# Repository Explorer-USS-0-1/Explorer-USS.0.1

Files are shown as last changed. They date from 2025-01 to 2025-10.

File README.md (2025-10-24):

# <p align="center"> EXPLORER USS.0.1 </p>

<p align="center">
 
</p>

The goal of this project is to create and learn how a exploration rover can be, how can be built and what we can do with it. We liked the idea to do something that could move anywhere we wanted, on every type of soil and very far away, so we designed and created our personal rover from scratch.

Because we couldn't see it everywhere, we gave to the rover an eye (a camera), so we can see what it sees.

Maybe is not a professional rover, or a competitive one, but for sure with a very limited budget and almost zero starting knowledge, we learned a lot about embedded software and IOT.

>[!Note]
>
>In the [printfile folder](/Rover_chassis_and_tools_printfiles) there are a lot of files, cause during the desing phase we scraped and redesinged a lot of time the rover prototype.

## REQUIREMENTS

#### Hardware

To build and use this project, you need the following hardware:

- 1x Texas Instruments MSP432P401R microcontroller
- 1x [Educational BoosterPack MKII](https://www.ti.com/tool/BOOSTXL-EDUMKII)
- 2x [Esp32-Wroom-32D](https://www.espressif.com/sites/default/files/documentation/esp32-wroom-32d_esp32-wroom-32u_datasheet_en.pdf)
- 1x [Esp32-CAM](https://media.digikey.com/pdf/Data%20Sheets/DFRobot%20PDFs/DFR0602_Web.pdf)
- 4x DC Motors (driving wheels)
- 2x L298N motor's driver
- 2x micro servomotor
- A 12 volt 3.5 Amp powersource (for the motor controller board)
- 2x 5 volt powersource (1 for the Esp-Cam, 1 for the Servomotors and Esp32)
  - If you want, you can use a voltage step down board (we did this due to time and budget costrains)
- 2x [rover track outer frame](Rover_chassis_and_tools_printfiles/ProtoTank_TrackOuterFrame.stl)
- 2x [rover track inner frame](Rover_chassis_and_tools_printfiles/ProtoTank_trackinnerFrame.stl)
- 2x [full rover tracks](Rover_chassis_and_tools_printfiles/track_1_5.stl)
- 6x [cog](Rover_chassis_and_tools_printfiles/ProtoTank_Cog.stl)
- [Rover base frame](Rover_chassis_and_tools_printfiles/ProtoTank_baseFrame.stl)
- 2x [L298N driver holder](Rover_chassis_and_tools_printfiles/L298N%20holder%20V3.stl)
- [Rover top frame](Rover_chassis_and_tools_printfiles/ProtoTank_TopFrame.stl)
- [Base for camera structure](Rover_chassis_and_tools_printfiles/CAMTANKFINAL.stl)
- [Pan & tilt arm base](Rover_chassis_and_tools_printfiles/Pan-tilt-plataforma_finale.stl)
- [Pan part for "turret"](Rover_chassis_and_tools_printfiles/Pan-tilt-tapa_finale.stl)
- [Tilt part for "turret"](Rover_chassis_and_tools_printfiles/platformafinalv2.3.stl)
- [Esp32-Cam holder](Rover_chassis_and_tools_printfiles/finalemnte%20v2.stl)
- [Power System Holder](Rover_chassis_and_tools_printfiles/power%20supply%20holder%20v4.stl)
- Jumper wires of all types (M/F , M/M , F/F)
- A lot of screws and bolts
- 1 Usb-C cable
- PLA of two different colors ( one for tracks, one for everything else)
<p align="center">
  

  

  
</p>

#### Software
- [Code Composer Studio](https://www.ti.com/tool/CCSTUDIO) Integrated Development Environment (IDE)
- [MSP432 DriverLib](https://www.ti.com/tool/download/SIMPLELINK-MSP432-SDK/3.40.01.02)
- Arduino IDE

>[!IMPORTANT]
>
>The rover is designed to be customizable, our project is just an example.

## PROJECT LAYOUT

```
├───Rover
│   ├───Esp32Cam
│   ├───Final
│   └───MSP + ESP FINAL
│       ├───Debug
│       │   └───LcdDriver
│       ├───LcdDriver
│       └───targetConfigs
├───Rover_chassis_and_tools_printfiles
└───Separate_testing_tools
    ├───Car_Image_State_Machine
    │   ├───Debug
    │   │   └───LcdDriver
    │   ├───LcdDriver
    │   └───targetConfigs
    ├───DC_Motors
    ├───MSP_Tank_Final
    │   ├───Debug
    │   │   └───LcdDriver
    │   ├───LcdDriver
    │   └───targetConfigs
    ├───MSP_Tank_Test
    │   ├───Debug
    │   │   └───LcdDriver
    │   ├───LcdDriver
    │   └───targetConfigs
    ├───Push_buttons
    │   ├───Debug
    │   │   └───LcdDriver
    │   ├───LcdDriver
    │   └───targetConfigs
    └───Servomotors
```

## SETUP

### Hardware setup

The hardware setup requires time and planning, because **all the structural part** of the rover are **3D printed**. We decided to do this to have a light but very strong structure.

>[!Note]
>
>The prints of our project were made with 100% recicled PLA.

#### ROVER

After printing all the files linked in the [**hardware requirements**](#REQUIREMENTS) section ( or any other file in the [Rover_chassis_and_tools_printfile](https://github.com/Dennis-Alberti/IoT-project/tree/main/Rover_chassis_and_tools_printfiles) folder), you can start build up the chassis in this order:
1. Build the track frames (whit the cogs), and put the DC motors in them;
   <p align="center">
        

2. Put the track frames on the baseframe, using screws and bolts to secure the 2 parts, and then put the L298N driver holders in the holes of the base (they should perfectly fit);
3. Use screw and bolts to secure the L298N divers to their holder frames; also connect the motors to the drivers and be sure that the opposing engines have the color order of the cables reversed. At the same time be sure that the motors sharing the track frame have the same cables color order;
    <p align="center">
        
    </p>
4. Use the F/F jumper wires to connect all the motor speed pins to the ESP32-2 (displayed in the [**PIN LAYOUT**](#PIN_LAYOUT) section, ESP32-2 table);
5. Close the chassis whit the rover top frame, then put the tracks in place;
6. Put inside the ESP32-Cam holder the ESP32-Cam, and then build up the "turret" structure with the servomotors;
    <p align="center">
      
    </p>
8. Mount on the rover chassis the "turret" and connect to the Esp32-2 the servomotors (following the same table of the point 4);
    <p align="center">
       
       
    </p>
9. Now is possible put any additional accessory or tool ( from our printfile folder or any custom-made one ).

>[!IMPORTANT]
>
>**To power up everything the same way we did it, check out the [POWER SYSTEM MANAGEMENT](#POWER_SYSTEM_MANAGEMENT) section**

#### JOYSTICK

Connect the MSP432P401R microcontroller whit the ESP32-1 using F/F Jumper wires, following the [ESP32-1 table pin layout](#PIN_LAYOUT).
  <p align="center">
   
  </p>

### Software setup

##### Msp432 Setup
1. Go to the section below (MSP432 DriverLib Setup) to setup the DriverLib to be able to use the [Educational BoosterPack MKII](https://www.ti.com/tool/BOOSTXL-EDUMKII).
2. Connect the MSP with a computer.
3. Go to [`Rover/MSP + ESP FINAL/main.c`](Rover/MSP%20%2B%20ESP%20FINAL/main.c), [`Rover/MSP + ESP FINAL/functions.h`](Rover/MSP%20%2B%20ESP%20FINAL/functions.h) and [`Rover/MSP + ESP FINAL/functions.c`](Rover/MSP%20%2B%20ESP%20FINAL/functions.c) and download the files.
4. Open it in the projects previously created at point 1.
5. Upload and run the code.

##### Esp32-1 Setup  
1. Connect the ESP with a computer.  
2. Go to [`Rover/Final/EspSender.ino`](Rover/Final/EspSender.ino) ,and download the file.   
3. Open it with Arduino IDE and change the variable `broadcastAddress[]` with the address of the ESP connected to the rover (*see [Communication Section](#COMMUNICATION)*).  
4. Upload and run the code.  

##### Esp32-2 Setup  
1. Connect the ESP with a computer.
2. Go to [`Rover/Final/DcandServo.ino`](Rover/Final/DcandServo.ino), and download the file. 
3. Open it with Arduino IDE and install the library: **"ESP32Servo"** by *Kevin Harrington, John K. Bennett*.  
4. Upload and run the code.

##### Esp32-Cam Setup
1. Connect the Esp-cam with a computer.
2. Go to [`Rover/Final/EspSender.ino`](Rover/Esp32Cam) ,download all the files in the folder and create a folder with all of them inside.
3. Open the CameraWebServerEsp32Cam.ino file with Arduino IDE. In the "const char *ssid" and "const char *password" variables (line 39 and 40 of the code) put the name and the password of the wi-fi you're going to use to host the webserver;
4. Upload and run the code.
5. Only for the first time (or everytime you change the host wi-fi), you have to copy the IP ADDRESS, printed in output on the Serial monitor of your pc, and paste it on a browser tab. 

Once you have ensured the connection between the 2 ESP32 (see [COMMUNICATION](#COMMUNICATION) section to know how), and the webserver for the ESP32-CAM is working, you can start to use the rover.
   
## HOW TO USE

The MSP432 code put in action the rover. The initial state shows a white car and the phrase "Welcome Back !". 

<p align="center">

</p>

To start moving the tank, press the S3 button (position right/bottom of the controller), that will put the joystick in TANK mode, displaying the current state on the screen. Now you can move the rover using the joystick.
* UP: move the rover forward.
* DOWN: move the rover backward.
* RIGHT: move the rover right.
* LEFT: move the rover left

<p align="center"> 

</p>

To use the camera and thus entering CAMERA mode, press the S2 button (position right/top of the controller) and use the joystick to point in the desired direction. 
* UP: move the camera up.
* DOWN: move the camera down.
* RIGHT: move the camera right.
* LEFT: move the camera left.
* JOYSTICK BUTTON: reset the camera position to the center.

Pressing the S2 button will the switch again to the TANK mode, and so on.
All this is possible thanks to the handler, that will listen for the interrupt of an action at any moment and send the message to the Esp32-1.

Now you can use EXPLORER USS.0.1 to go everywhere you want, and see what your eyes could never!

>[!Note]
>
> Is possible to test every part of the project separatley, just go in the in the [separate_testing_tools](/Separate_testing_tools) folder, and try whatever you want (for the rover parts, you will need to implememt an external joystick for testing, but not the full one).

## COMMUNICATION

This project is divided into two modules: the **controller** and the **rover**. These modules are connected via ESP-NOW protocol using two ESP32 microcontrollers. All the information originates from the MSP432 microcontroller, which sends it to **ESP32-1**. ESP32-1 then transmits the data to **ESP32-2**, which interprets the messages and sends instructions to the DC motors and servo motors on the rover. The connection between the ESP's is done using the libraries <esp_now.h> and <WiFi.h> in Arduino IDE. 

The decision to use the ESP-NOW protocol is due to the reliability, low energy consumption, high message transfer speed and long range connection.

>[!IMPORTANT]
>
>To set up and use ESP-NOW you need to know the IP address of the Rover's ESP32. Here's a quick tutorial how: https://randomnerdtutorials.com/get-change-esp32-esp8266-mac-address-arduino/

To establish communication between the MSP432 and ESP32-1, we had three options: **I2C**, **UART**, and **SPI**. We chose **UART** because it requires fewer pins and is simpler to implement. Due to the pin layout of the MSP432, we are limited to using UART module **A2**, with pins **3.2 (Rx)** and **3.3 (Tx)**, connected to pins **17 (TX)** and **16 (Rx)** respectively. 

The UART is configured to use the **SMCLK (Sub-Main Clock)** for the following reasons:
1. We are using a low baud rate of **9600**, which does not require a high-frequency clock.
2. Using SMCLK allows the **main clock (MCLK)** to operate independently, freeing it up for other tasks.
3. There is no need to use the main clock, as it is less power-efficient compared to SMCLK.

This setup ensures efficient and reliable communication between the MSP432 and ESP1 while optimizing power consumption and resource allocation.

## PIN LAYOUT

 Table 1: ESP32 connected to MSP432
| **ESP32 Pin** | **MSP432 Pin** | 
|---|---|
| GPIO16 (RX) | P3.3 (TX) | 
| GPIO17 (TX) | P3.2 (RX) |
| GND | GND |
| VIN | 5V | 

 Table 2: ESP32 connected to DC motors and servo motors
| **ESP32 Pin** | **DC motors** | **Servo motors** | **Power System** |
|---|---|---|---|
| 21 | Motor1 Pin1 | - | - |
| 33 | Motor1 Pin2 | - | - |
| 16 | Motor2 Pin1 | - | - |
| 17 | Motor2 Pin2 | - | - |
| 18 | Motor3 Pin1 | - | - |
| 19 | Motor3 Pin2 | - | - |
| 22 | Motor4 Pin1 | - | - |
| 23 | Motor4 Pin2 | - | - |
| 27 | MOTOR1 SPEED | - | - |
| 26 | MOTOR2 SPEED | - | - |
| 14 | MOTOR3 SPEED | - | - |
| 25 | MOTOR4 SPEED | - | - |
| 13 | - | servoX (Signal)  | - |
| 32 | - | servoY (Signal)  | - |
| GND | - | - | GND |
| VIN | - | - | 5V |

 Table 3: MSP432 Pins Axis Joystick with Push Buttons
| **Pin Functions**  | **MSP432 Pin** | 
|--- |---|
| Hori X-axis | P6.0	 | 
| Verti Y-axis | P4.4 |
| Select button | P4.1 |
| S2 button | P5.1 | 
| S3 button | P3.5 | 

## MSP432 DriverLib Setup

First thing to perform is setting up the IDE. For this purpose use [Code Composer Studio](https://www.ti.com/tool/CCSTUDIO) Integrated Development Environment (IDE) and:
- Create a new project, select the MSP432P401R board in the selection tab and give a name to the project.
- Download and extract the [MSP432 DriverLib](https://www.ti.com/tool/download/SIMPLELINK-MSP432-SDK/3.40.01.02) and save in a reachable directory, then do the following action to setup the environment:
   
1. Extract simplelink_msp432p4_sdk_3_40_01_02.zip file.
2. Open CCS and left click on Project Folder to select Properties
3. Select CCS Build
4. Click ARM Compiler and then Include Options
5. Add "simplelink_msp432p4_sdk_3_40_01_02/source" directory to "Add dir to #include search path" window.  
6. Click ARM Linker and File Search Path
7. Add "simplelink_msp432p4_sdk_3_40_01_02/source/ti/devices/msp432p4xx/driverlib/ccs/msp432p4xx_driverlib.lib" to "Include library file..." window

## POWER SYSTEM MANAGEMENT

The power system of our rover it's composed by 4 modules:
1. A 12 Volt 3.5 Ah module to power up the L298N drivers for DC motors. This was obtained by putting in series 8 batteries of 1.5 Volt;
2. A 9 Volt battery connected to a step down voltage board  to power up the servomotors and the ESP32-2;
3. A 5 Volt output powerbank to power up the ESP32-Cam (we decided to do this because the camera drains a lot of power);
4. A 5 volt output powerbank to power up the MSP432 and the connected ESP32-1. 

The first 2 modules are powering up motors connected and controlled by the ESP32-2, so they have to share in common the ground. To do it, we placed the stepdown voltage board on a breadboard using the external channels, which are connected per row throughout the breadboard.
In this way we made a row where the electricity output of the step down board was off, putting instead the external 12 Volt module, and connecting in the parallel row the grounds from the ESP32-2, from the L298N drivers and from the servomotors. In the other external row we set a 5V electricity output so we could power up the ESP32-2 trough the VIN pin and the 2 servomotors (the ESP32 pinout is already described in the [*Communication*](#COMMUNICATION) section).
<p align="center">

</p>

Table 4: Rover power system management  
| **DC motors** | **Servo motors** | **Stepdown board** |
|---|---|---|
| Power | - | 12V - 3.5A (output off) |
| GND | - | GND | 
| - | Power | 5V  (output on) |
| - | GND | GND |

## Link to powerpoint and Youtube video
- Youtube [video](https://youtu.be/4N75zm8ps9I)
- Powerpoint [presentation](https://docs.google.com/presentation/d/1o49VAeFgKbm6rYsIu1tgTplBiTX86RdQqd6DO4X7Q_E/edit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)

## ISSUES.

In this section we want to explain the major difficulties encountered during the project.

One of the main drawbacks was using the MSP432 as a controller. In fact we noticed that the command input had some latency, approximately 500ms. This was also due to the UART connection between the MSP432 and ESP32, followed by the connection via the ESP-NOW protocol. Also using the MSP432 boosterpack limited the possibility to have simultameous movement of camera and rover. But we decided to use the board anyway to challenge us into understanding more complicated boards than Arduino.

Another problem was the lack of knowledge in the field of electronic engineering. In fact we had no prior knowledge about the hardware and power management parts, so we had to study from zero how these worked.

The last drawback was the limited budget, that forced us to use low-cost hardware.

## FUTURE IMPROVEMENTS

- Rebuilding the power system, using only a rechargable Lipo battery to power every part of the rover;
- Upgrading the quality of the sensors, of the motors and of the camera;
- Using only 2 ESP's, one for the controller and one for the movement;
- Implementing simultaneous movement of camera and rover, and also have more freedom in the movements;
- Implementing an automated movement system using ultrasonic sensors and algorithms;
- Implementing an object detection project using the camera;
- Implementing an automated garage for the rover, working as an homestation where it can recharge;
- Implementing some led light, to use the rover also in darker places;
- Implementing a more detailed interface on screen, by creating a menu screen to navigate through the different modes;
- Implementing a timer to register inactivity from the user, causing the system to switch to a sleep mode;
- Using the Pulse Width Modulation to regulate the movement speed based on the position of the controller ( so constantly changing , and not a fixed value);
- Optimize the code; make the code easier to read, more intuitive.

## TEAM MEMBERS

The project was developed in a team and the code was divided into many different areas (Rover, Communications, Graphics, Hardware, ...); each member focused therefore only on certain aspects of the project.

- Riccardo Ferro (Leader)
  - Contributed mainly to the creation of the physical and hardware part of the rover. He designed the layout of the chassis, organized the power system and setted up all the connections of the rover. He also contributed a lot to write the code for motor control (ESP32-2) and also the code for the communication between ESP32-1 and ESP32-2 using the ESP-NOW protocol. He also did the ESP-32 Camera configuration and the final code and documantation review.

- Henrique Graça
  - Contributed mainly to: setup the ESP32-2 connection of the rover; write the code of the ESP32-2 and ESP32-1; UART connection between the MSP432 and ESP32-1. 

- Dennis Alberti
  - Contributed mainly in the creation of the MSP432 code.

- Tiago Silva
  - Contributed mainly in the creation of the MSP432 code and was responsible for video editting of the project's showcase.

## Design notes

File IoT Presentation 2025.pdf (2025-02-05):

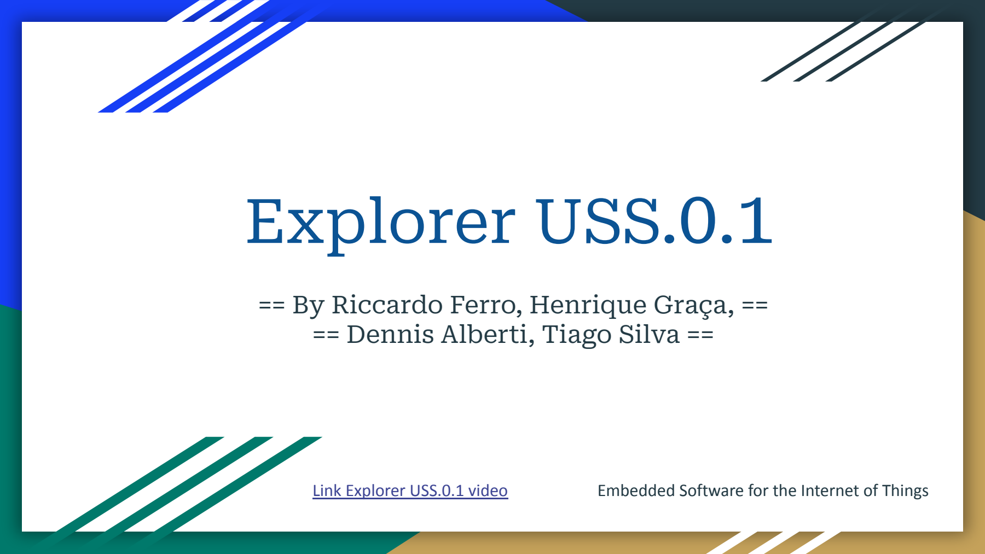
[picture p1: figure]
Explorer USS.0.1; == Dennis Alberti, Tiago Silva ==

## == By Riccardo Ferro, Henrique Graça, ==

Link Explorer USS.0.1 video (https://youtu.be/4N75zm8ps9I) | Embedded Software for the Internet of Things (https://didatticaonline.unitn.it/dol/auth/shibboleth/index.php)

## ROVER & CAMERA - CONTROLLER

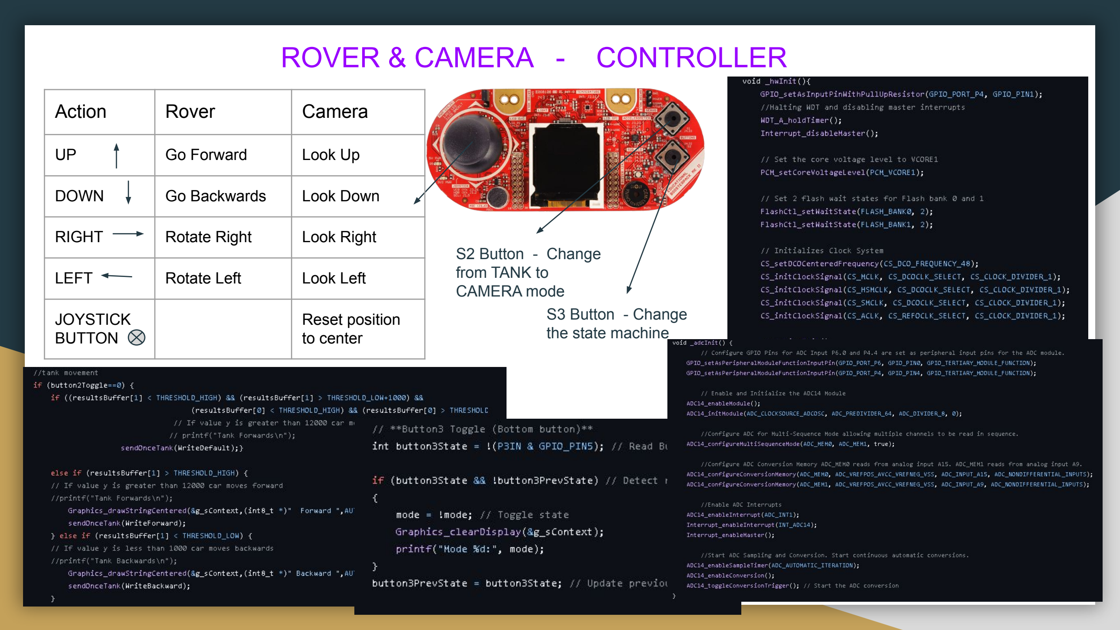
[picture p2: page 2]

S3 Button - Change
the state machine

S2 Button - Change
from TANK to
CAMERA mode
Action | Rover | Camera
UP | Go Forward | Look Up
DOWN | Go Backwards | Look Down
RIGHT | Rotate Right | Look Right
LEFT | Rotate Left | Look Left
JOYSTICK BUTTON | | Reset position to center

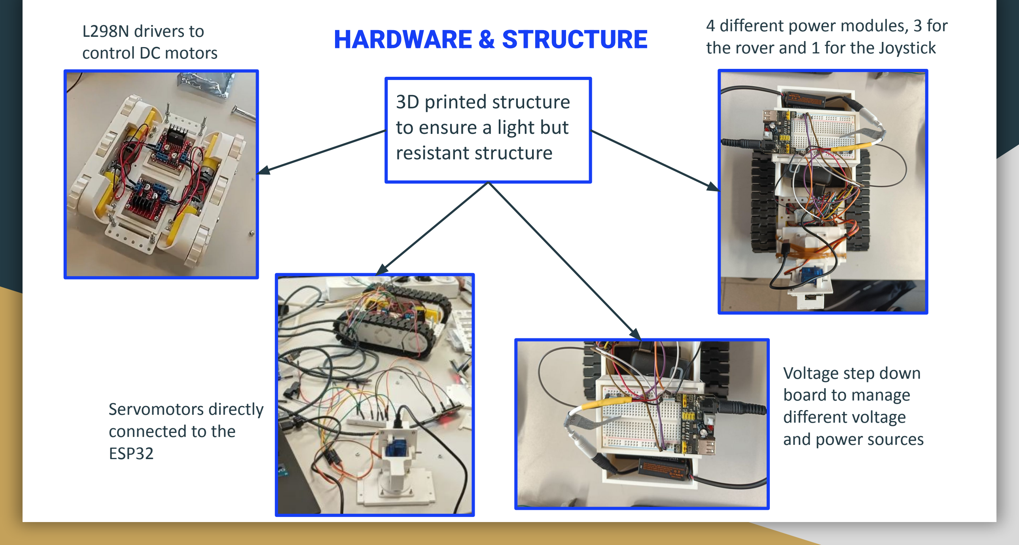
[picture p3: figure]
HARDWARE & STRUCTURE L298N drivers to control DC motors; 4 different power modules, 3 for the rover and 1 for the Joystick; 3D printed structure to ensure a light but resistant structure; Servomotors directly connected to the ESP32; Voltage step down board to manage different voltage and power sources

## MOTORS,DRIVERS AND CAMERA

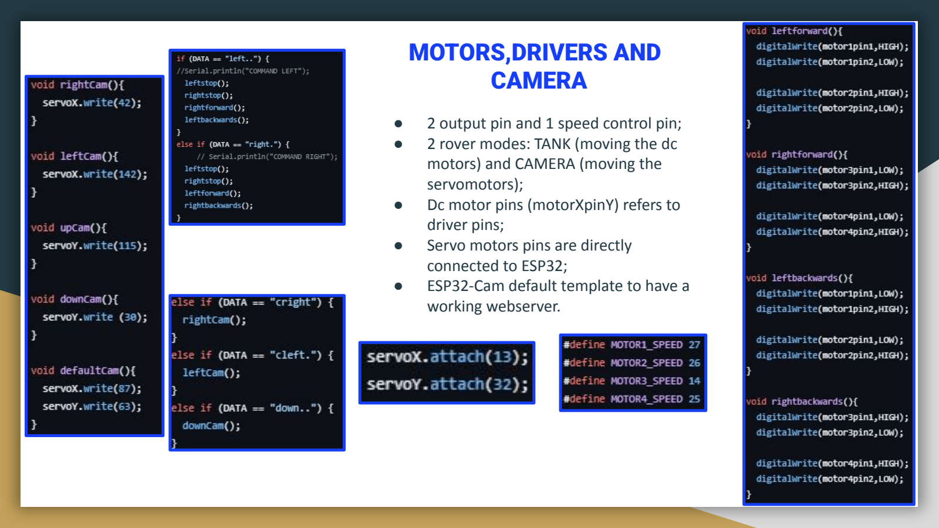
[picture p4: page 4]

- 2 output pin and 1 speed control pin;
- 2 rover modes: TANK (moving the dc motors) and CAMERA (moving the servomotors);
- Dc motor pins (motorXpinY) refers to driver pins;
- Servo motors pins are directly connected to ESP32;
- ESP32-Cam default template to have a working webserver.

## COMMUNICATION MSP

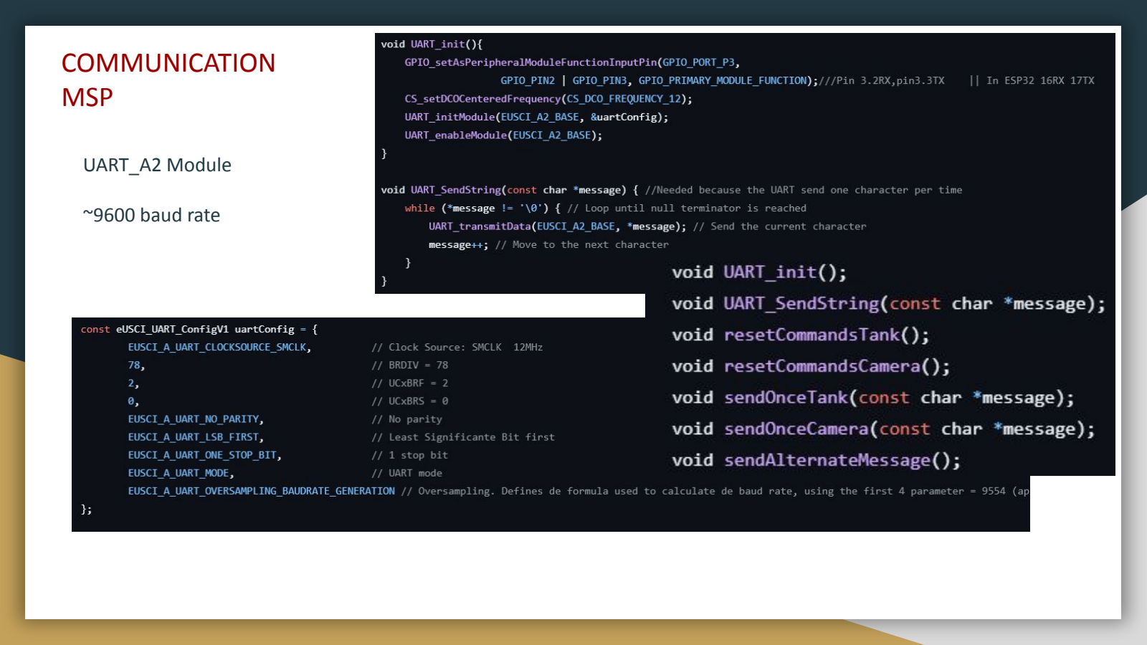
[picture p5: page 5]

UART_A2 Module

~9600 baud rate

## COMMUNICATION

## ESP1

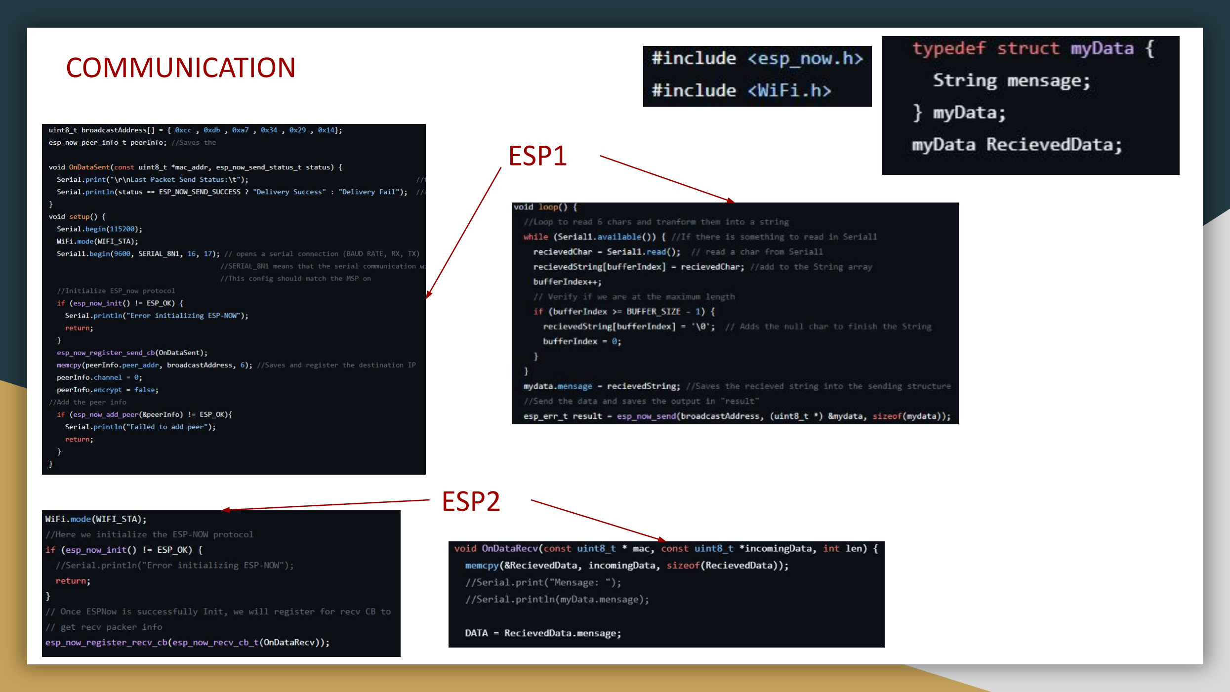
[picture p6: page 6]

## ESP2

## TESTING & FUTURE IMPROVEMENT

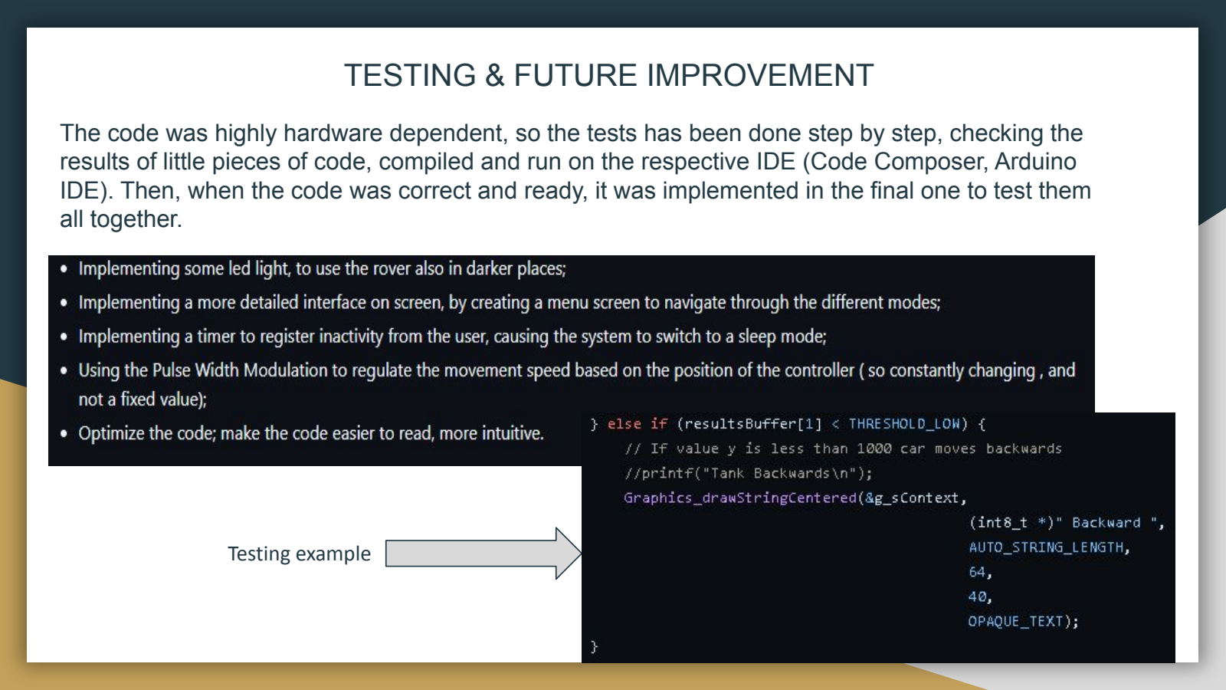
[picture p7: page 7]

The code was highly hardware dependent, so the tests has been done step by step, checking the results of little pieces of code, compiled and run on the respective IDE (Code Composer, Arduino IDE). Then, when the code was correct and ready, it was implemented in the final one to test them all together.

Testing example

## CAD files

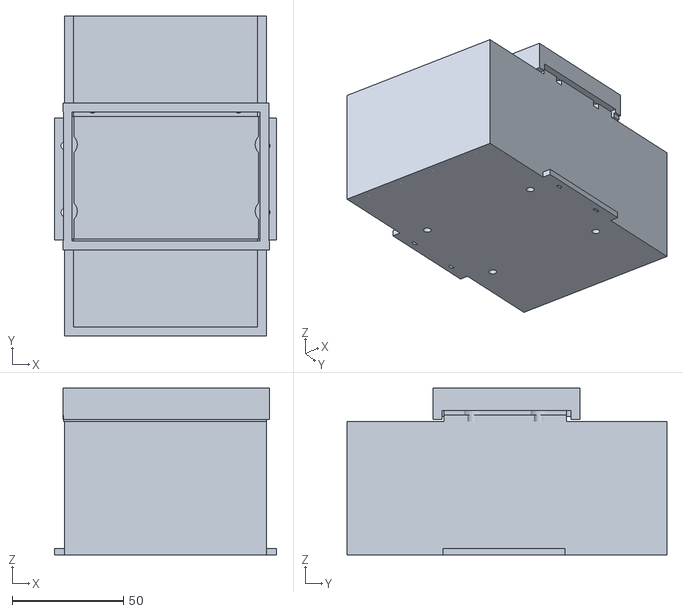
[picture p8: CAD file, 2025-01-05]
Rover_chassis_and_tools_printfiles/powersupply holder v3.stl
100.0 x 144.0 x 75.1

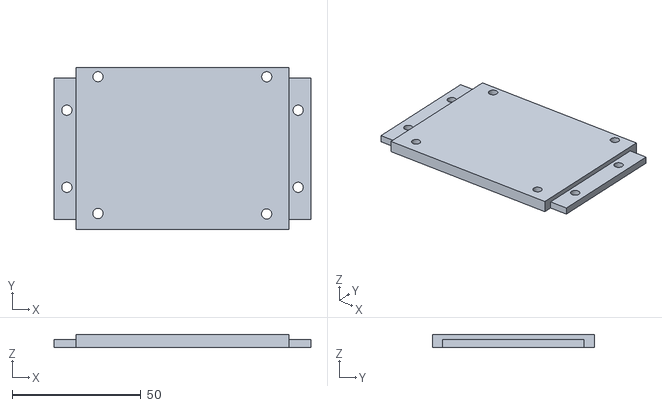
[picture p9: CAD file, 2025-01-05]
Rover_chassis_and_tools_printfiles/Powering System Base.stl
100.0 x 63.2 x 5.00

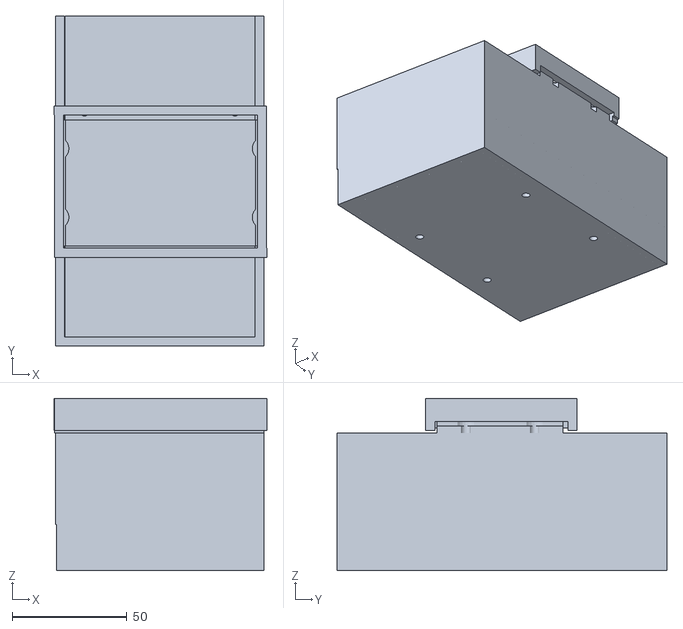
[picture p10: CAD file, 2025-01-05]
Rover_chassis_and_tools_printfiles/power supply holder v4.stl
92.9 x 144.0 x 75.1

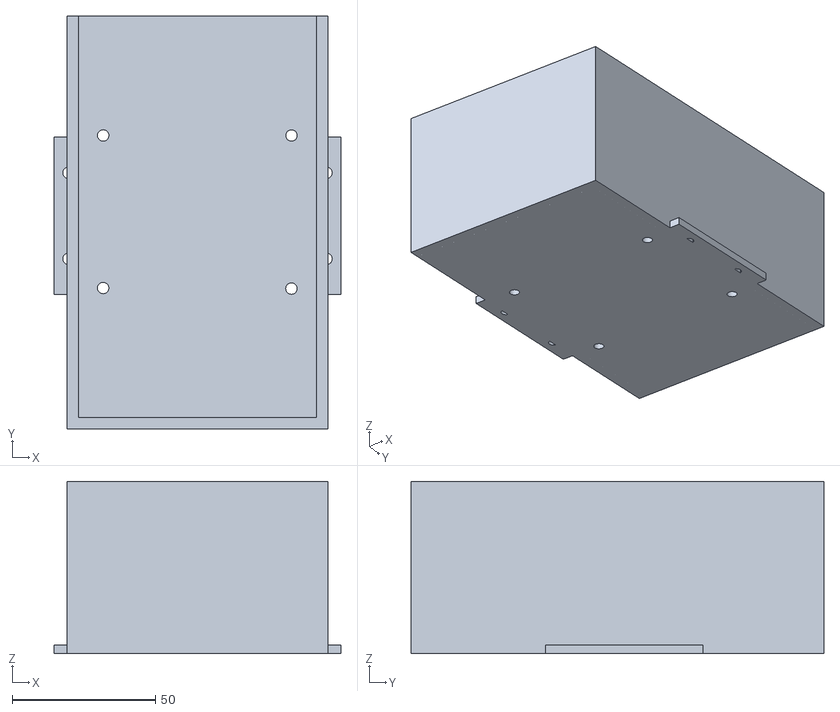
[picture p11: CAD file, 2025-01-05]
Rover_chassis_and_tools_printfiles/temporary power system holder.stl
100.0 x 144.0 x 60.0

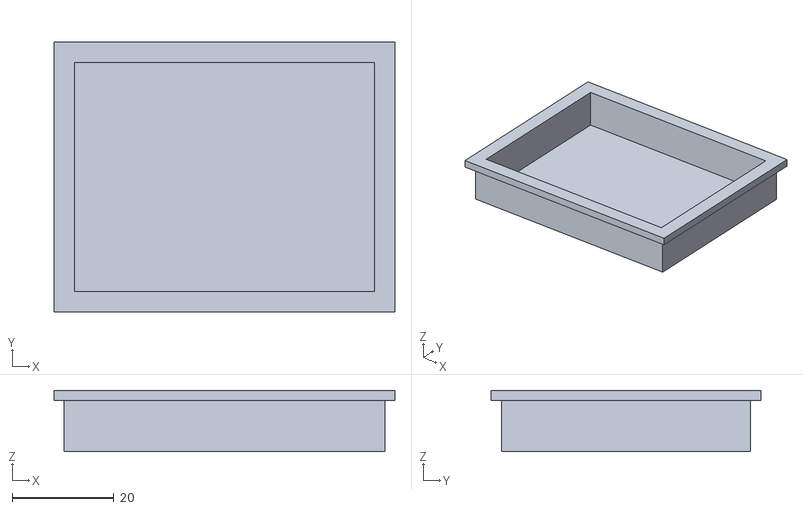
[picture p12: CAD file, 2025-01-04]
Rover_chassis_and_tools_printfiles/Accessory_baseTray.stl
67.0 x 53.0 x 12.0

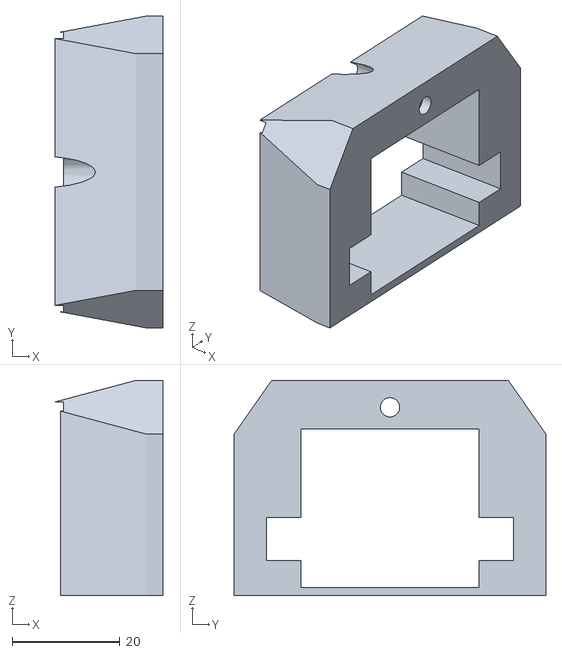
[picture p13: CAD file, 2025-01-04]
Rover_chassis_and_tools_printfiles/CAMERACOVE V$.stl
20.0 x 58.0 x 40.0

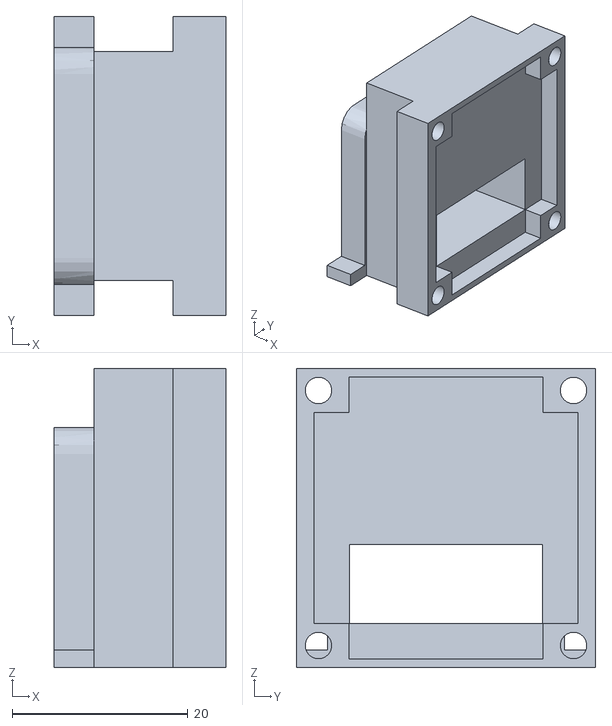
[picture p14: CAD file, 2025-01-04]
Rover_chassis_and_tools_printfiles/My Cmaera holder v1.stl
19.6 x 34.0 x 34.0

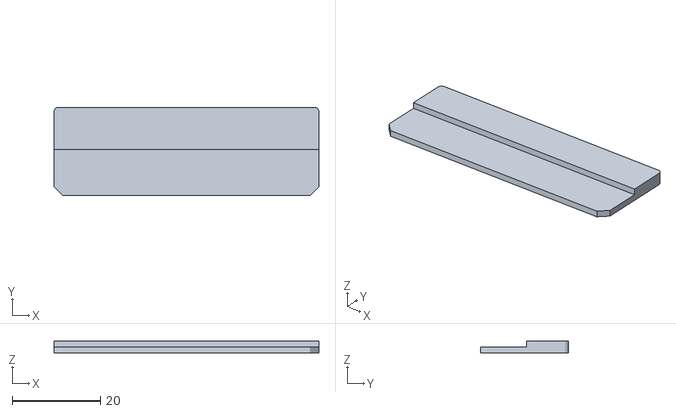
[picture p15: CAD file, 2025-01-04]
Rover_chassis_and_tools_printfiles/TheBackFellOffItsNotSupposedToDoThat.stl
60.0 x 20.0 x 2.80

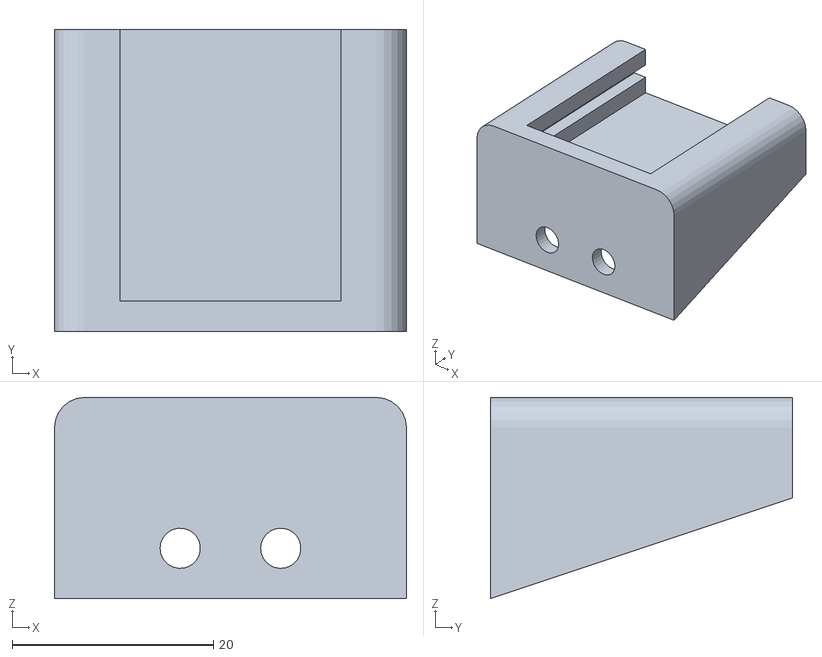
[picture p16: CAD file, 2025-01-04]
Rover_chassis_and_tools_printfiles/Accessory_Static_RPi_CameraHolder.stl
35.0 x 30.0 x 20.0

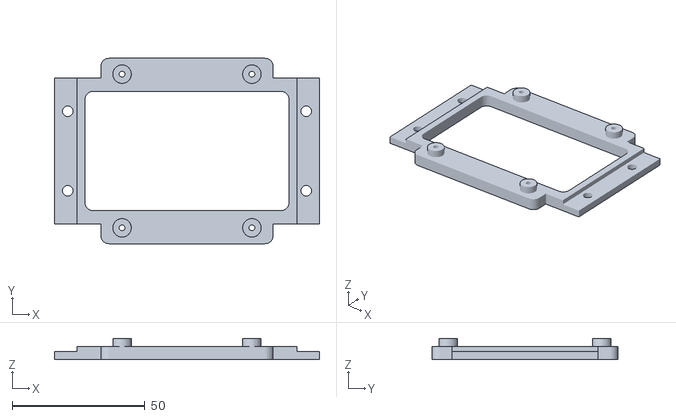
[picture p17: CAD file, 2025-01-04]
Rover_chassis_and_tools_printfiles/Accessory_RPiHolder.stl
100.0 x 70.0 x 8.00

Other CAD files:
Separate_testing_tools/Car_Image_State_Machine/Debug/LcdDriver/Crystalfontz128x128_ST7735.obj
Separate_testing_tools/MSP_Tank_Final/Debug/LcdDriver/Crystalfontz128x128_ST7735.obj
Separate_testing_tools/MSP_Tank_Test/Debug/LcdDriver/Crystalfontz128x128_ST7735.obj
Separate_testing_tools/Push_buttons/Debug/LcdDriver/Crystalfontz128x128_ST7735.obj
Separate_testing_tools/Car_Image_State_Machine/Debug/LcdDriver/HAL_MSP_EXP432P401R_Crystalfontz128x128_ST7735.obj
Separate_testing_tools/MSP_Tank_Final/Debug/LcdDriver/HAL_MSP_EXP432P401R_Crystalfontz128x128_ST7735.obj
Separate_testing_tools/MSP_Tank_Test/Debug/LcdDriver/HAL_MSP_EXP432P401R_Crystalfontz128x128_ST7735.obj
Separate_testing_tools/Push_buttons/Debug/LcdDriver/HAL_MSP_EXP432P401R_Crystalfontz128x128_ST7735.obj
Rover/MSP + ESP FINAL/Debug/LcdDriver/Crystalfontz128x128_ST7735.obj
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

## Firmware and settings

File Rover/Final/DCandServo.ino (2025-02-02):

#include <esp_now.h>
#include <WiFi.h>
#include <ESP32Servo.h>

#define MOTOR1_SPEED 27
#define MOTOR2_SPEED 26
#define MOTOR3_SPEED 14
#define MOTOR4_SPEED 25

Servo servoX;
Servo servoY;

// Structure example to receive data
// Must match the sender structure
typedef struct myData {
  String mensage;
} myData;
myData RecievedData;

int motor1pin1 = 21;
int motor1pin2 = 33;
int motor2pin1 = 16;
int motor2pin2 = 17;
int motor3pin1 = 18;
int motor3pin2 = 19;
int motor4pin1 = 22;
int motor4pin2 = 23;

String DATA;


void OnDataRecv(const uint8_t * mac, const uint8_t *incomingData, int len) {
  memcpy(&RecievedData, incomingData, sizeof(RecievedData));
  //Serial.print("Mensage: ");
  //Serial.println(myData.mensage);

  DATA = RecievedData.mensage;

    if (DATA == "left..") {
    //Serial.println("COMMAND LEFT");
      leftstop();
      rightstop();
      rightforward();
      leftbackwards();
    }
    else if (DATA == "right.") {
         // Serial.println("COMMAND RIGHT");
      leftstop();
      rightstop();
      leftforward();
      rightbackwards();
    } 
    else if (DATA == "forwar") {
          //Serial.println("COMMAND UP");
      leftstop();
      rightstop();
      rightforward();
      leftforward();
    }
    else if (DATA == "backwa") {
          //Serial.println("COMMAND DOWN");
      leftstop();
      rightstop();
      rightbackwards();
      leftbackwards();
    }
    else if(DATA == "defaul"){
      leftstop();
      rightstop();
    }
    else if (DATA == "cright") {
      rightCam();
    }
    else if (DATA == "cleft.") {
      leftCam();
    }
    else if (DATA == "down..") {
      downCam();
    }
    else if (DATA == "up....") {
      upCam();
    }
    else if (DATA == "middle") {
      defaultCam();
    }
}  
/* SPEED CONTROLS; SAVE IF NEEDED LATER
  if(speed_control == 1){
      analogWrite(MOTOR1_SPEED,255);
      analogWrite(MOTOR2_SPEED,255);
      analogWrite(MOTOR3_SPEED,255);
      analogWrite(MOTOR4_SPEED,255);
  }
  else{
      analogWrite(MOTOR1_SPEED,200);
      analogWrite(MOTOR2_SPEED,200);
      analogWrite(MOTOR3_SPEED,200);
      analogWrite(MOTOR4_SPEED,200);
  }*/

//THESE ARE THE FUNCTIONS TO MAKE THE CAMERA MOVE
void rightCam(){
  servoX.write(42);
}

void leftCam(){
  servoX.write(142);
}

void upCam(){
  servoY.write(115);
}

void downCam(){
  servoY.write (30);
}

void defaultCam(){
  servoX.write(87);
  servoY.write(63);
}

//THESE ARE THE FUNCTIONS TO MAKE THE ROVER MOVE
void leftforward(){
  digitalWrite(motor1pin1,HIGH);
  digitalWrite(motor1pin2,LOW);

  digitalWrite(motor2pin1,HIGH);
  digitalWrite(motor2pin2,LOW);
}

void rightforward(){
  digitalWrite(motor3pin1,LOW);
  digitalWrite(motor3pin2,HIGH);
  
  digitalWrite(motor4pin1,LOW);
  digitalWrite(motor4pin2,HIGH);
}

void leftbackwards(){
  digitalWrite(motor1pin1,LOW);
  digitalWrite(motor1pin2,HIGH);

  digitalWrite(motor2pin1,LOW);
  digitalWrite(motor2pin2,HIGH);
}

void rightbackwards(){
  digitalWrite(motor3pin1,HIGH);
  digitalWrite(motor3pin2,LOW);

  digitalWrite(motor4pin1,HIGH);
  digitalWrite(motor4pin2,LOW);
}

void rightstop(){
  digitalWrite(motor1pin1,LOW);
  digitalWrite(motor1pin2,LOW);

  digitalWrite(motor2pin1,LOW);
  digitalWrite(motor2pin2,LOW);
}

void leftstop(){
  digitalWrite(motor3pin1,LOW);
  digitalWrite(motor3pin2,LOW);

  digitalWrite(motor4pin1,LOW);
  digitalWrite(motor4pin2,LOW);
}

void setup() {
  //these are the pin settings for the DC motors
  pinMode(motor1pin1, OUTPUT);
  pinMode(motor1pin2, OUTPUT);
  pinMode(motor2pin1, OUTPUT);
  pinMode(motor2pin2, OUTPUT);
  pinMode(motor3pin1, OUTPUT);
  pinMode(motor3pin2, OUTPUT);
  pinMode(motor4pin1, OUTPUT);
  pinMode(motor4pin2, OUTPUT);
  
  pinMode(MOTOR1_SPEED, OUTPUT);
  pinMode(MOTOR2_SPEED, OUTPUT);
  pinMode(MOTOR3_SPEED, OUTPUT);
  pinMode(MOTOR4_SPEED, OUTPUT);

  analogWrite(MOTOR1_SPEED,200);
  analogWrite(MOTOR2_SPEED,200);
  analogWrite(MOTOR3_SPEED,200);
  analogWrite(MOTOR4_SPEED,200);

  //These are the pin settings for the servomotors
  servoX.attach(13);
  servoY.attach(32);
  servoX.write(87);
  servoY.write(63);

  Serial.begin(115200);
  
  WiFi.mode(WIFI_STA);

  //Here we initialize the ESP-NOW protocol
  if (esp_now_init() != ESP_OK) {
    //Serial.println("Error initializing ESP-NOW");
    return;
  }
  
  // Once ESPNow is successfully Init, we will register for recv CB to
  // get recv packer info
  esp_now_register_recv_cb(esp_now_recv_cb_t(OnDataRecv));
}

void loop() {
 
}

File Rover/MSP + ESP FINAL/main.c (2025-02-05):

#include <ti/devices/msp432p4xx/inc/msp.h>
#include <ti/devices/msp432p4xx/driverlib/driverlib.h>
#include <ti/grlib/grlib.h>
#include "LcdDriver/Crystalfontz128x128_ST7735.h"
#include <stdio.h>
#include <string.h>
#include <stdbool.h>
#include "msp.h"

#include "functions.h"

#define THRESHOLD_HIGH 12000
#define THRESHOLD_LOW 1000

// Graphics library context
Graphics_Context g_sContext;

// ADC results buffer
volatile int mode = 0;
volatile uint16_t resultsBuffer[2];

// Initialize buttons state values to 0
volatile int button2Toggle = 0; // Toggles for Button2
volatile int button2PrevState = 0; // Previous state of Button2
volatile int button3Toggle = 0; // Toggles for Button2
volatile int button3PrevState = 0; // Previous state of Button2


// Function prototypes
void _graphicsInit();
void _adcInit();
void _hwInit();
void drawCar(void);
void fn_IMAGE(void);
void ADC14_IRQHandler(void);

// ----------------------------------- GENERAL INITS --------------------------------------

// Graphics initialization function
void _graphicsInit() {
    // Initialize the display
    Crystalfontz128x128_Init();
   Crystalfontz128x128_SetOrientation(LCD_ORIENTATION_UP);

    // Initialize the graphics context
    Graphics_initContext(&g_sContext, &g_sCrystalfontz128x128, &g_sCrystalfontz128x128_funcs);
    Graphics_setForegroundColor(&g_sContext, GRAPHICS_COLOR_WHITE);
    Graphics_setBackgroundColor(&g_sContext, GRAPHICS_COLOR_BLACK);
    Graphics_clearDisplay(&g_sContext);
    GrContextFontSet(&g_sContext, &g_sFontFixed6x8);
}

// ADC initialization
void _adcInit() {
        // Configure GPIO Pins for ADC Input P6.0 and P4.4 are set as peripheral input pins for the ADC module.
    GPIO_setAsPeripheralModuleFunctionInputPin(GPIO_PORT_P6, GPIO_PIN0, GPIO_TERTIARY_MODULE_FUNCTION);
    GPIO_setAsPeripheralModuleFunctionInputPin(GPIO_PORT_P4, GPIO_PIN4, GPIO_TERTIARY_MODULE_FUNCTION);
        
        // Enable and Initialize the ADC14 Module
    ADC14_enableModule();
    ADC14_initModule(ADC_CLOCKSOURCE_ADCOSC, ADC_PREDIVIDER_64, ADC_DIVIDER_8, 0);
        
        //Configure ADC for Multi-Sequence Mode allowing multiple channels to be read in sequence.
    ADC14_configureMultiSequenceMode(ADC_MEM0, ADC_MEM1, true);
        
        //Configure ADC Conversion Memory ADC_MEM0 reads from analog input A15. ADC_MEM1 reads from analog input A9.
    ADC14_configureConversionMemory(ADC_MEM0, ADC_VREFPOS_AVCC_VREFNEG_VSS, ADC_INPUT_A15, ADC_NONDIFFERENTIAL_INPUTS);
    ADC14_configureConversionMemory(ADC_MEM1, ADC_VREFPOS_AVCC_VREFNEG_VSS, ADC_INPUT_A9, ADC_NONDIFFERENTIAL_INPUTS);
        
        //Enable ADC Interrupts
    ADC14_enableInterrupt(ADC_INT1);
    Interrupt_enableInterrupt(INT_ADC14);
    Interrupt_enableMaster();

        //Start ADC Sampling and Conversion. Start continuous automatic conversions. 
    ADC14_enableSampleTimer(ADC_AUTOMATIC_ITERATION);
    ADC14_enableConversion();
    ADC14_toggleConversionTrigger(); // Start the ADC conversion
}

void _hwInit(){
    GPIO_setAsInputPinWithPullUpResistor(GPIO_PORT_P4, GPIO_PIN1);
    //Halting WDT and disabling master interrupts
    WDT_A_holdTimer();
    Interrupt_disableMaster();

    // Set the core voltage level to VCORE1
    PCM_setCoreVoltageLevel(PCM_VCORE1);

    // Set 2 flash wait states for Flash bank 0 and 1
    FlashCtl_setWaitState(FLASH_BANK0, 2);
    FlashCtl_setWaitState(FLASH_BANK1, 2);

    // Initializes Clock System
    CS_setDCOCenteredFrequency(CS_DCO_FREQUENCY_48);
    CS_initClockSignal(CS_MCLK, CS_DCOCLK_SELECT, CS_CLOCK_DIVIDER_1);
    CS_initClockSignal(CS_HSMCLK, CS_DCOCLK_SELECT, CS_CLOCK_DIVIDER_1);
    CS_initClockSignal(CS_SMCLK, CS_DCOCLK_SELECT, CS_CLOCK_DIVIDER_1);
    CS_initClockSignal(CS_ACLK, CS_REFOCLK_SELECT, CS_CLOCK_DIVIDER_1);

    _graphicsInit();
    _adcInit();
}


// Function to draw a car
void drawCar() {
    //Graphics_clearDisplay(&g_sContext);
    Graphics_drawRectangle(&g_sContext, &(Graphics_Rectangle){20, 50, 100, 70}); // Car body
    Graphics_drawLine(&g_sContext, 30, 50, 50, 30);  // Left slanted line
    Graphics_drawLine(&g_sContext, 50, 30, 80, 30);  // Top horizontal line
    Graphics_drawLine(&g_sContext, 80, 30, 100, 50); // Right slanted line
    Graphics_drawCircle(&g_sContext, 35, 75, 10);  // Left wheel
    Graphics_drawCircle(&g_sContext, 85, 75, 10);  // Right wheel
    Graphics_drawStringCentered(&g_sContext, (int8_t *)"Welcome back!", AUTO_STRING_LENGTH, 64, 110, OPAQUE_TEXT);
}

// IMAGE state
void fn_IMAGE() {
        printf("We are in IMAGE MODE");
        //Graphics_clearDisplay(&g_sContext);
        Graphics_setBackgroundColor(&g_sContext, GRAPHICS_COLOR_BLACK);
        Graphics_setForegroundColor(&g_sContext, GRAPHICS_COLOR_WHITE);

        drawCar();
        //event = SW_NONE;
    }


// -----------------------------------MAIN FUNCTION --------------------------------------

int8_t *x = (int8_t *)"Neutral ";
int8_t *y = (int8_t *)"Neutral ";

/* MAIN FUNCTION  */
void main(void) {
    WDT_A->CTL = WDT_A_CTL_PW | WDT_A_CTL_HOLD; // Stop the watchdog

    _hwInit();
    // startButtonInit();
    UART_init();
    sendOnceTank(WriteTank);


    while (1) {
        PCM_gotoLPM0(); // Enter low-power mode
    }
}
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

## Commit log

2024-11-18 Making folder for servomotors
2024-11-18 Create CameraWebServerEsp32Cam
2025-02-03 refactoring the layout
    [Crystalfontz128x128_ST7735.obj, HAL_MSP_EXP432P401R_Crystalfontz128x128_ST7735.obj]
